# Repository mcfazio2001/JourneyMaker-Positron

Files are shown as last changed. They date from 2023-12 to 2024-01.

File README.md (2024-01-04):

<div align="center">

# JourneyMaker-Positron
voxolite

https://voxolite.com/

IMG_3391_(1)

## Our Discord
<br>

</div>

## About

JourneyMaker is a redesigned 3D printer that combines the best qualities of [Positron V3](https://github.com/KRALYN/PositronV3) and [Positron LT](https://github.com/Audiotronix/Positron_LT) with our own innovations. Perfect for hobbyists and professionals looking for a space-saving printing solution.

Built upon the innovative Positron V3 form factor and motion system by [KRALYN](https://github.com/KRALYN/PositronV3) and inspired by the Positron LT design, the JourneyMaker represents a combination of their standout features with our unique improvements. Many of the design improvements to the Positron printer come from the LT, while JourneyMaker integrates those into its own design. JourneyMaker simplifies all design complexities from the other Positron versions and enhances performance to make it the best Positron Printer available. 

Its compatibility with modifications tailored for other Positron versions makeing it an ideal choice for an enhanced printing experience while allowing flexibility for personalized adjustments.

</div>

## Advantages 

- Simplified assembly (The easiest Positron Printer to build)
- Cost reduction (Cost less than the Positron V3) 
- User-friendly build guide
- Integrated PSU (power supply unit) with 200W
- 3mm GT2 timing belt on XY (cheaper and easier to source than the original Synchromesh wire)
- Simplified Z axis by using a leadscrew. Easy to assemble by folding up
- Improved tool head cooling and heat creep
- Readily available machined parts (No need to machine your parts, we've got you covered. Vist Voxolite.com)
- Less machined parts than the Positron V3
- New extruder

</div>

## Specs

-	Max Print Speed: `250mm/s` (Not limited to)
-	Max Travel Speed: `350mm/s` (Not limited to)
-	Acceleration: `9800mm/s^2` (Not limited to)
-	Build Volume: `180x180x173mm`
-	Weight: `2600-3000g` (with integrated PSU)
-	Hotend max temp: `250C`
-	Build Plate Max temp: `80-100C`
-	Power supply: `24V; 200W`
-	Footprint: `~200mmx200mm`

</div>
<br>

## Build Instructions and Bill of Materials 
  
Link for the BOM:
https://docs.google.com/spreadsheets/d/1nYiwHz63ZsrtXtIAmWYqItgidqx7duSCUeQ9fUIy6CY/edit?usp=sharing

Link for the Instructions:
https://docs.google.com/presentation/d/1X3SdqvoahyYstLh0CLl6Gt2k5lkNw0UiuemN1DqQ030/edit?usp=sharing

</div>
<br>

## Help Support the Project 
If you like this design, please consider supporting the Voxolite team via donations; [Paypal](https://www.paypal.com/donate/?hosted_button_id=8HVCJBN4Q7MXC)

</div>
<br>

## License
<be>

General Overview:

- License Type: Creative Commons Attribution-NonCommercial 4.0 International.
- Licensing Entity: Creative Commons Corporation.
  
Important Definitions:

- Adapted Material: Material derived from or based upon the Licensed Material, requiring permission under the Copyright and Similar Rights.
- Licensed Material: The original work, database, or material covered by the license.

Scope of License:

- **License Grant: You are granted a worldwide, royalty-free, non-sublicensable, non-exclusive, irrevocable license for NonCommercial purposes only.**
- Exceptions and Limitations: The license does not apply if Exceptions and Limitations to Copyright and Similar Rights are in effect.
- Media and Formats: You are authorized to exercise the Licensed Rights in all media and formats, with technical modifications allowed.
- Downstream Recipients: Recipients automatically receive an offer to exercise the Licensed Rights.

License Conditions:

- **Attribution: If you share the material, you must provide attribution to the creator(s) and others designated, indicating modifications and license terms. This condition extends to Adapted Material.**

Sui Generis Database Rights:

- Specifics: Additional conditions apply if the Licensed Rights include Sui Generis Database Rights.

Disclaimer and Limitation of Liability:

- Warranties: The licensor provides the material as-is and makes no warranties.
- Limitation of Liability: The licensor is not liable for any losses, costs, or damages arising from the use of the material.

Term and Termination:

- Term: The license applies for the term of the Copyright and Similar Rights.
- Termination: Your rights terminate automatically if you fail to comply, but they can be reinstated under certain conditions.

Other Terms and Conditions:

- Additional Terms: The licensor is not bound by additional or different terms unless expressly agreed.

Interpretation:

- Non-Reduction: The license does not reduce, limit, or impose conditions on any lawful use without permission.
- Enforceability: Unenforceable provisions are automatically reformed or severed without affecting the rest.
- No Waiver: No waiver of terms or conditions unless expressly agreed.

Immunities:

- Privileges and Immunities: Nothing in the license limits the privileges and immunities that apply to the Licensor or You.

Important Note:

This summary is not a substitute for the actual license text, and it's crucial to read and understand the complete license terms for compliance. If you have specific questions or concerns, it's advisable to seek legal advice or consult the Creative Commons website.

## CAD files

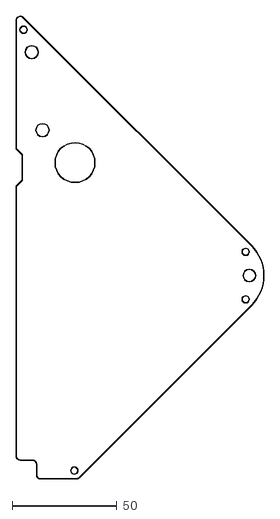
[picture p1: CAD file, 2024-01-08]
JourneyMaker STL Files/DXF Files (Optional)/TopPlate_Right.dxf
118.0 x 220.6

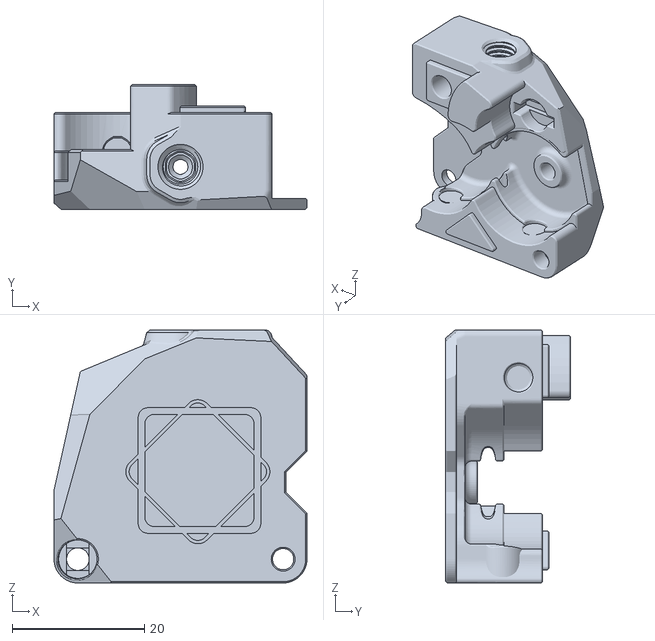
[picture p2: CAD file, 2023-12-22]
JourneyMaker STL Files/Extruder/Hummingbird_extruder_mod2 parts - Front_PC4_M6-1.stl
38.2 x 18.8 x 38.2

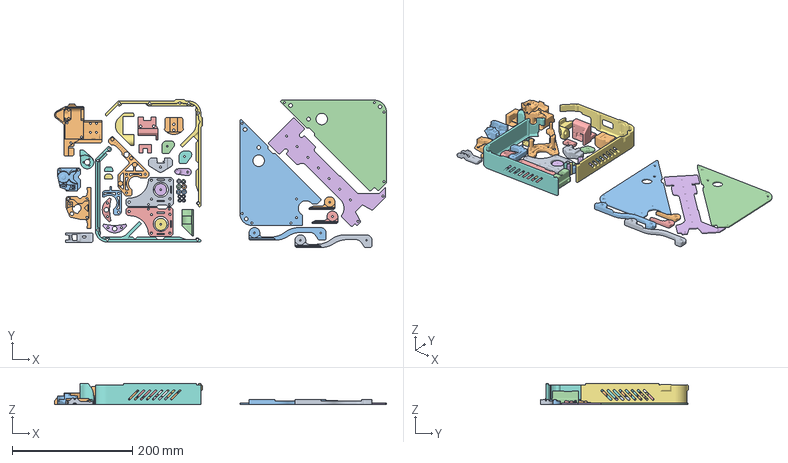
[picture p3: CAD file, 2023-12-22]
JourneyMaker STL Files/JourneyMaker.3mf
551.5 x 245.8 x 35.5 mm
Belt_Tensioner_XY V2.2 - Belt_Tensioner_XY.stl
Front_Pannel (1).stl
M3 x8.3_Spacers - M3 x11.5_Spacers.stl x 4
M3x5_Spacers (1).stl x 2
RasingClamp_For_BedHolder_Left (1).stl
RasingClamp_For_BedHolder_Left (2).stl
Side_Pannel_Left - Side_Pannel_Left.stl
Side_Pannel_Right - Side_Pannel_Right.stl
Spacer_3.2ID_6OD - Spacer_3.2ID_6OD.stl x 4
Tool Head (1).stl
TopPlate_Left_V2 - TopPlate_Left.stl
TopPlate_Right_V2 - TopPlate_Right.stl
Z Axis Bed Holder Connection (Mag Connector) - Z Axis Bed Holder Connection v3.stl
Z Axis Tensioner - Z Axis Tensioner.stl
Z Axis Top Mount (1).stl
Z Carriage Mount v2.2 - Z Carriage Mount.stl
x-axis_Motor_Bracket_v2 - x-axis_Motor_Bracket_Left.stl
z-Axis_Motor_Bracket Copy 1 - z-axis_Motor_Bracket.stl
z-Axis_Motor_Bracket Copy 1 - z-axis_Motor_TopPlate_Support.stl
z-axis-LeaderScrew_Bottom_Mount (2).stl
x-axis_Motor_Bracket_v2 - x-axis_Motor_Bracket_Right.stl
Belt connector (1).stl
Bed_Clamp - Bed_Clamp.stl x 2
SpoolHolder Part 3.stl x 2
SpoolHolder Part 2.stl x 2
SpoolHolder Part 1.stl x 2
Center_Pannel - PCB Cover.stl
x-Rail_Endcap (1).stl x 2
Hummingbird_extruder_mod2 parts - Arm^Hummingbird_extruder_5.stl
Hummingbird_extruder_mod2 parts - Back.stl
Hummingbird_extruder_mod2 parts - Front_PC4_M6-1.stl

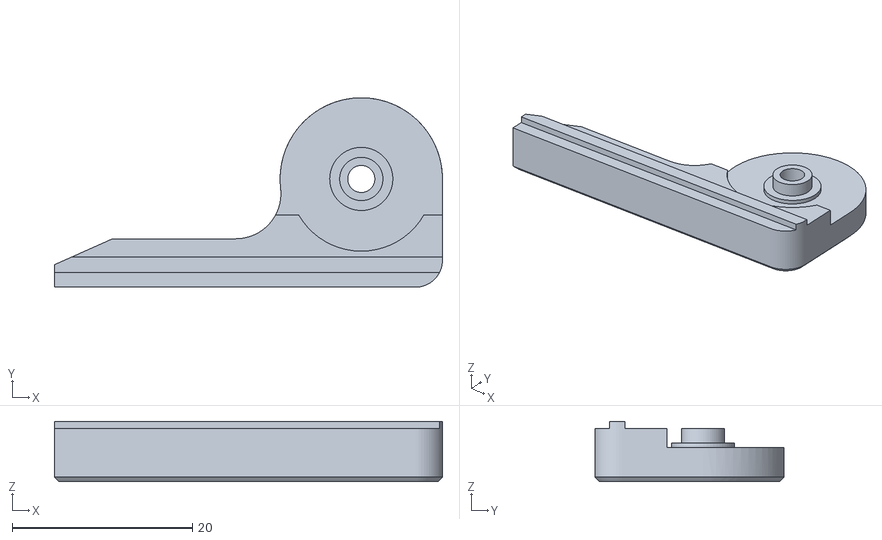
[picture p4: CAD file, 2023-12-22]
JourneyMaker STL Files/Spool_Holder/SpoolHolder Part 1.stl
43.0 x 21.0 x 6.70

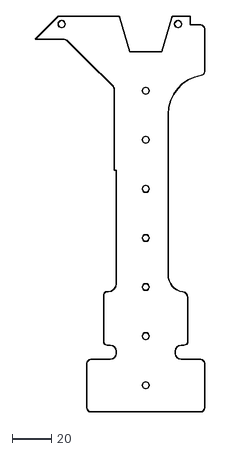
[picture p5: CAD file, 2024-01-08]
JourneyMaker STL Files/DXF Files (Optional)/Center_Pannel.dxf
86.2 x 201.6

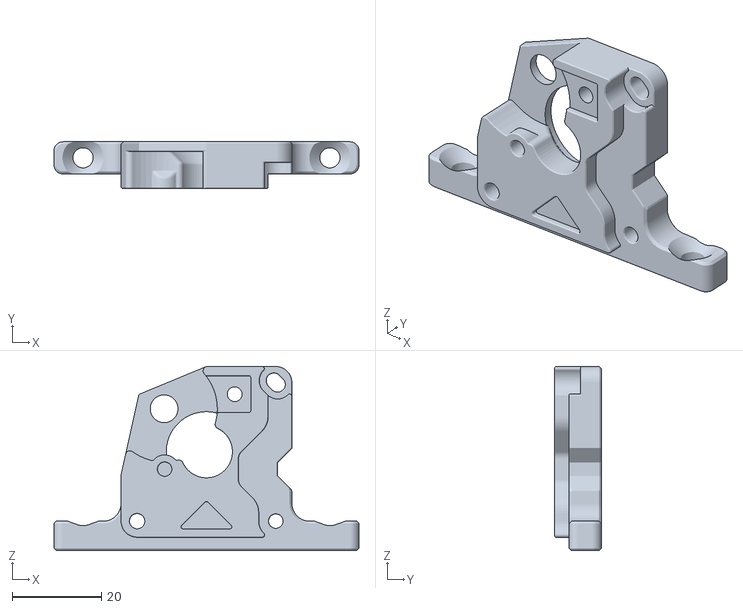
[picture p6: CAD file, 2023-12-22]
JourneyMaker STL Files/Extruder/Hummingbird_extruder_mod2 parts - Back.stl
68.2 x 10.4 x 41.2

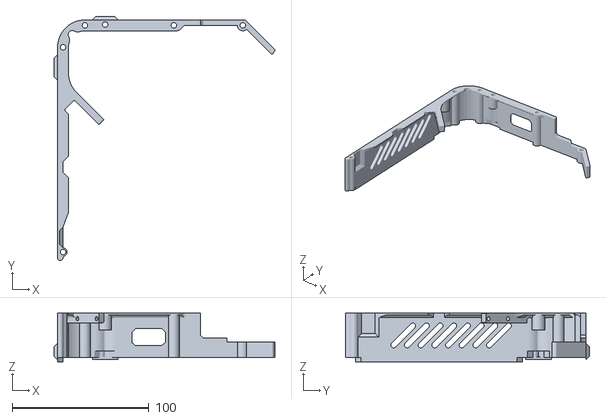
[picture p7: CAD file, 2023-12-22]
JourneyMaker STL Files/Main Parts/Side_Pannel_Left - Side_Pannel_Left.stl
161.3 x 178.3 x 35.5

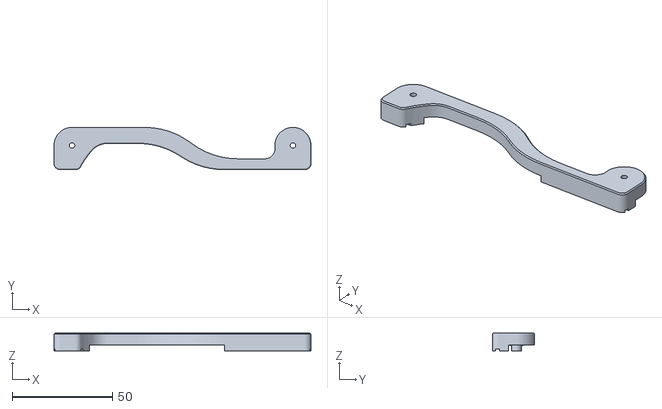
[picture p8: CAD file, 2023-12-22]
JourneyMaker STL Files/Spool_Holder/SpoolHolder Part 2.stl
128.0 x 21.0 x 8.90

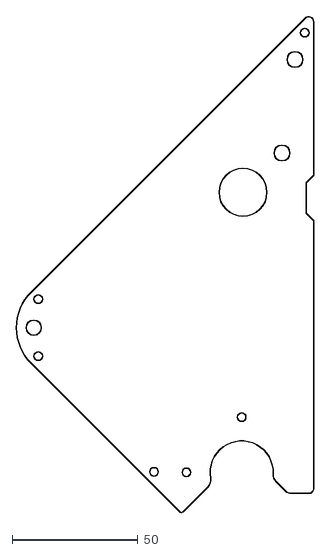
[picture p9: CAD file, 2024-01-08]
JourneyMaker STL Files/DXF Files (Optional)/TopPlate_Left.dxf
118.0 x 197.2

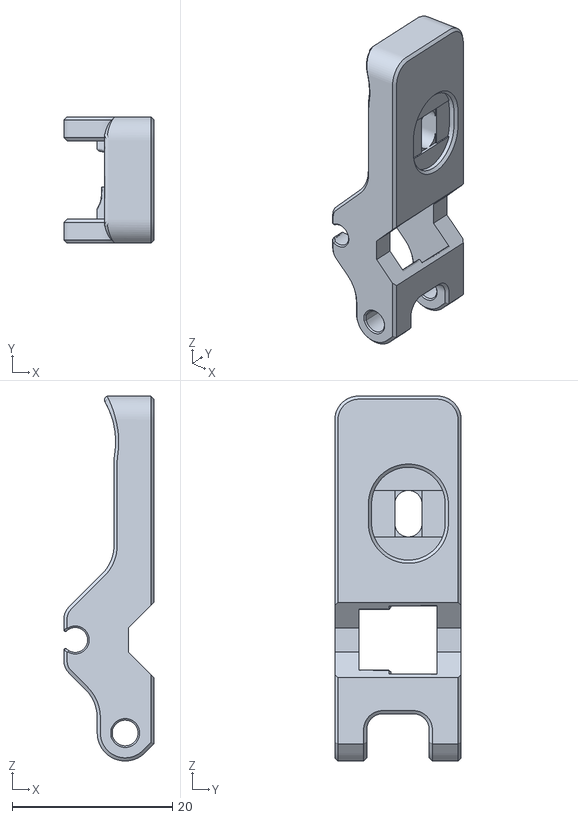
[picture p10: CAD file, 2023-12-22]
JourneyMaker STL Files/Extruder/Hummingbird_extruder_mod2 parts - Arm^Hummingbird_extruder_5.stl
11.2 x 15.8 x 45.6

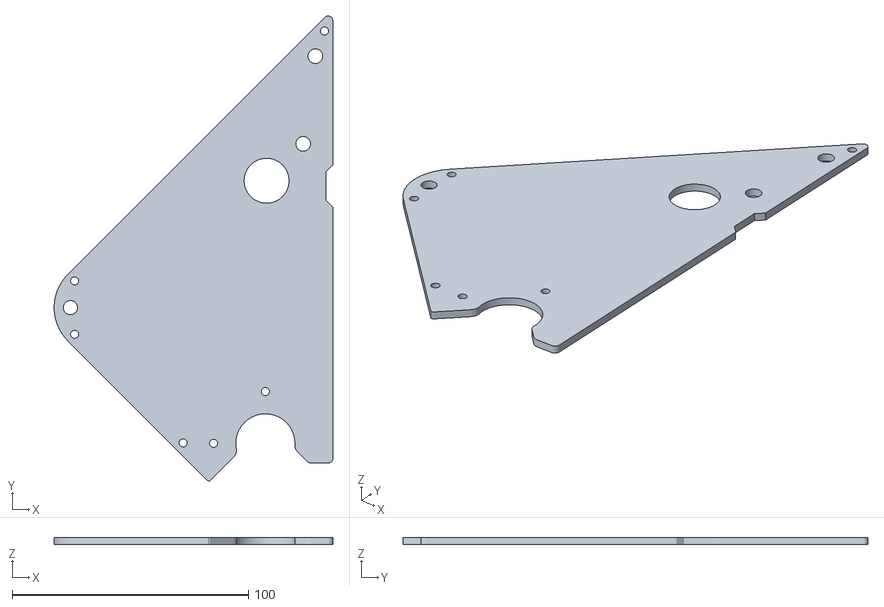
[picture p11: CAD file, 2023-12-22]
JourneyMaker STL Files/Main Parts/TopPlate_Left_V2 - TopPlate_Left.stl
118.0 x 196.9 x 3.00

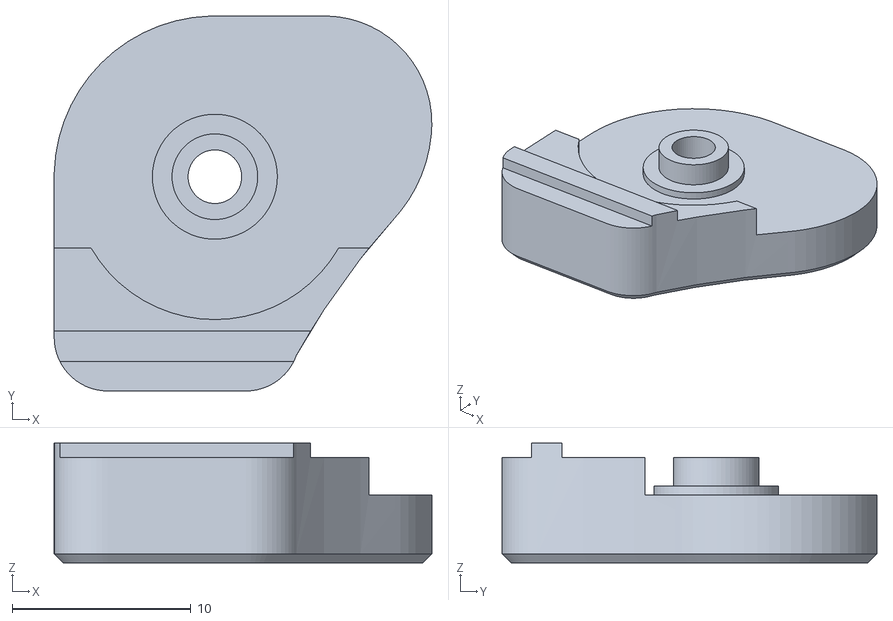
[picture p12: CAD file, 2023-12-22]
JourneyMaker STL Files/Spool_Holder/SpoolHolder Part 3.stl
21.1 x 21.0 x 6.70

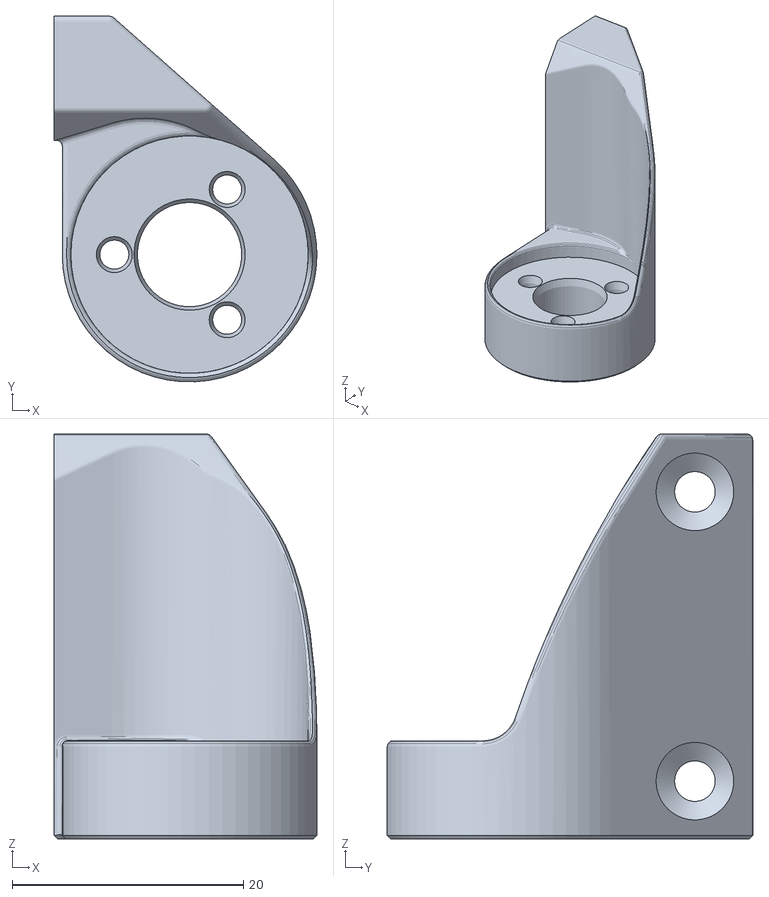
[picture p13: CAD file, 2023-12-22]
JourneyMaker STL Files/Main Parts/Z Carriage Mount v2.2 - Z Carriage Mount.stl
22.7 x 31.6 x 35.0

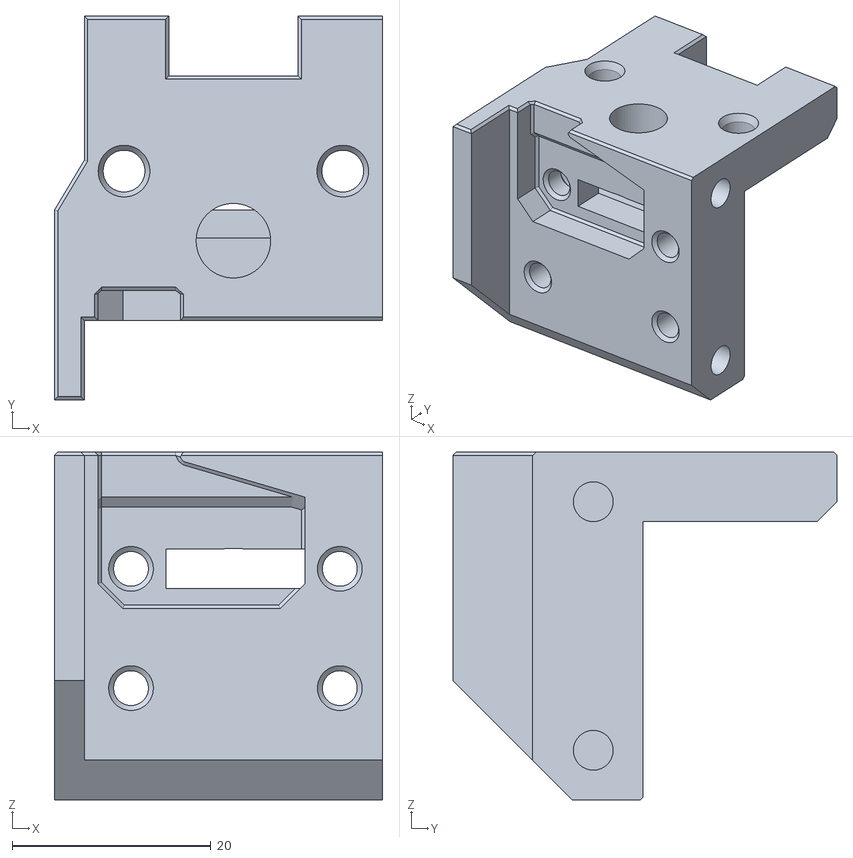
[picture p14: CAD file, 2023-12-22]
JourneyMaker STL Files/Main Parts/Z Axis Bed Holder Connection (Mag Connector) - Z Axis Bed Holder Connection v3.stl
33.0 x 38.6 x 35.0

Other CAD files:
JourneyMaker STL Files/Main Parts/TopPlate_Right_V2 - TopPlate_Right.stl
JourneyMaker STL Files/Main Parts/Spacer_3.2ID_6OD - Spacer_3.2ID_6OD.stl
JourneyMaker STL Files/Main Parts/RasingClamp_For_BedHolder_Left (1).stl
JourneyMaker STL Files/Main Parts/x-axis_Motor_Bracket_v2 - x-axis_Motor_Bracket_Right.stl
JourneyMaker STL Files/Main Parts/Bed_Clamp - Bed_Clamp.stl
JourneyMaker STL Files/Main Parts/Belt connector (1).stl
JourneyMaker STL Files/Main Parts/Belt_Tensioner_XY V2.2 - Belt_Tensioner_XY.stl
JourneyMaker STL Files/Main Parts/Center_Pannel - PCB Cover.stl
JourneyMaker STL Files/Main Parts/Front_Pannel (1).stl
JourneyMaker STL Files/Main Parts/M3 x8.3_Spacers - M3 x11.5_Spacers.stl
JourneyMaker STL Files/Main Parts/M3x5_Spacers (1).stl
JourneyMaker STL Files/Main Parts/RasingClamp_For_BedHolder_Left (2).stl
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

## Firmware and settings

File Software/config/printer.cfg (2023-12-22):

[include mainsail.cfg]

[printer]
kinematics: corexy
max_velocity: 500
max_accel: 15000
max_accel_to_decel: 10000
square_corner_velocity: 5 
max_z_velocity: 50
max_z_accel: 200

[mcu]
serial: /dev/serial0
baud: 250000
restart_method: command

[stepper_y]
step_pin: gpio11
dir_pin: gpio10
enable_pin: !gpio12
microsteps: 16
rotation_distance: 40
endstop_pin: tmc2209_stepper_y:virtual_endstop
homing_retract_dist: 0
position_endstop: 0
position_max: 170
homing_speed: 20
#homing_positive_dir: True

[tmc2209 stepper_y]
uart_pin: gpio9
tx_pin: gpio8
uart_address: 0
run_current: 0.7
stealthchop_threshold: 999999
diag_pin: ^gpio4
driver_SGTHRS: 45

[stepper_x]
step_pin: gpio6
dir_pin: gpio5
enable_pin: !gpio7
microsteps: 16
rotation_distance: 40
endstop_pin: tmc2209_stepper_x:virtual_endstop
homing_retract_dist: 0
position_endstop: 0
position_max: 185
homing_speed: 20

[tmc2209 stepper_x]
uart_pin: gpio9
tx_pin: gpio8
uart_address: 2
run_current: 0.7
stealthchop_threshold: 999999
diag_pin: ^gpio3
driver_SGTHRS: 35

[stepper_z]
step_pin: gpio19
dir_pin: gpio28
enable_pin: !gpio2
microsteps: 16
rotation_distance: 4
endstop_pin: probe:z_virtual_endstop
position_min: -2.5
position_max: 173
homing_speed: 5

[tmc2209 stepper_z]
uart_pin: gpio9
tx_pin: gpio8
uart_address: 1
run_current: 0.4
stealthchop_threshold: 999999

[extruder]
step_pin: gpio14
dir_pin: !gpio13 #change this for direction
enable_pin: !gpio15
microsteps: 16

###V2 Extruder
full_steps_per_rotation: 200
rotation_distance: 53.494165  
gear_ratio: 44:10, 37:17

#rotation_distance: 4.92 #v1 Extruder

nozzle_diameter: 0.4
filament_diameter: 1.75
heater_pin: gpio23 
sensor_type: Generic 3950
sensor_pin: gpio27
control: pid
pid_Kp: 25.12
pid_Ki: 1.073
pid_Kd: 147
min_temp: -100
max_temp: 260
max_extrude_cross_section:2
pressure_advance: 0.43 #0.32
min_extrude_temp: 170 #0 for testing 
max_extrude_only_distance: 400

[tmc2209 extruder]
uart_pin: gpio9
tx_pin: gpio8
uart_address: 3
run_current: 0.69
hold_current: 0.4
stealthchop_threshold: 999999

[heater_bed]
heater_pin: gpio21
sensor_type: ATC Semitec 104NT-4-R025H42G
sensor_pin: gpio26
pwm_cycle_time: 0.015
max_power: 1.0
control: pid
pid_Kp: 56.852
pid_Ki: 2.1
pid_Kd: 383.75
min_temp: -100
max_temp: 85

[controller_fan mcu_fan]
pin: gpio17
max_power: 0.8
shutdown_speed: 0
cycle_time: 0.01
kick_start_time: 1
fan_speed: 0.8
idle_timeout: 5
stepper: stepper_x, stepper_y, stepper_z


[heater_fan nozzle_cooling_fan]
pin: gpio20
max_power: 0.7
kick_start_time: 1
shutdown_speed: 0

[fan]
pin: gpio18
kick_start_time: 1
max_power: 0.9
shutdown_speed: 0

[force_move]
enable_force_move = true

[gcode_macro FORCE_Z_UP]
gcode: FORCE_MOVE STEPPER=stepper_z DISTANCE=30 VELOCITY=40

[virtual_sdcard]
path: /home/3dprinter/printer_data/gcodes

[probe]
pin: ^gpio25
x_offset:55
y_offset: 30
#z_offset: 0.8
speed: 3
samples: 3
sample_retract_dist: 0.7

[bed_tilt]
points: 
  4, 14
  130, 14
  130, 100
  35, 100
speed: 150
horizontal_move_z: 4

[gcode_arcs]
resolution: 1.0

[homing_override]
gcode: # Please manually set Homing speed to about half of rotation_distance (28 for synchromesh positron)
  {% set HOME_CUR = 1.000 %} # higher current on steppers makes sensorless homing more reliable
  {% set HOME_SENS_X_AXIS = 35 %} #Set this value for stepper sensitivity during X-Axis Homing
  {% set HOME_SENS_Y_AXIS = 35 %} #Set this value for stepper sensitivity during Y-Axis Homing
  # Retrieve used setting for stepper current and save them
  {% set RUN_CUR_X_STEPPER = printer.configfile.settings['tmc2209 stepper_x'].run_current %}
  {% set RUN_CUR_Y_STEPPER = printer.configfile.settings['tmc2209 stepper_y'].run_current %}
  # Retrieve used setting for stepper sensitivity and save them
  {% set RUN_SENS_X_STEPPER = printer.configfile.settings['tmc2209 stepper_x'].driver_sgthrs %}
  {% set RUN_SENS_Y_STEPPER = printer.configfile.settings['tmc2209 stepper_y'].driver_sgthrs %}
  # Set current for sensorless homing
  SET_TMC_CURRENT STEPPER=stepper_x CURRENT={HOME_CUR}
  SET_TMC_CURRENT STEPPER=stepper_y CURRENT={HOME_CUR}
  # Pause to ensure driver stall flag is clear
  G4 P500
  #Make printer believe we are at 0 0 0 so we can move Y axis back towards center later
  SET_KINEMATIC_POSITION X=0
  SET_KINEMATIC_POSITION Y=0
  SET_KINEMATIC_POSITION Z=0
  # Home X
  SET_TMC_FIELD STEPPER=stepper_x FIELD=SGTHRS VALUE={HOME_SENS_X_AXIS}
  SET_TMC_FIELD STEPPER=stepper_y FIELD=SGTHRS VALUE={HOME_SENS_X_AXIS}
  G28 X0
  G0 X10 F5000
  G4 P500
  # Home Y
  SET_TMC_FIELD STEPPER=stepper_x FIELD=SGTHRS VALUE={HOME_SENS_Y_AXIS}
  SET_TMC_FIELD STEPPER=stepper_y FIELD=SGTHRS VALUE={HOME_SENS_Y_AXIS}
  G28 Y0
  G0 Y10 F5000
  G4 P500
  # Home Z
  G0 X100 Y100 F5000
  G28 Z0
  # Set current back to regular values because we don't need to print with the higher currents on motors
  SET_TMC_CURRENT STEPPER=stepper_x CURRENT={RUN_CUR_X_STEPPER}
  SET_TMC_CURRENT STEPPER=stepper_y CURRENT={RUN_CUR_Y_STEPPER}
  # Set sensitivity back to regular values
  SET_TMC_FIELD STEPPER=stepper_x FIELD=SGTHRS VALUE={RUN_SENS_X_STEPPER}
  SET_TMC_FIELD STEPPER=stepper_y FIELD=SGTHRS VALUE={RUN_SENS_Y_STEPPER}


[gcode_macro UNLOAD_FILAMENT]
gcode:
  M83 
  G1 E-30 F1800
  G1 E-100 F1200
  G1 E-100 F1200
  G1 E-100 F1200
  G1 E-100 F1200
  G1 E-100 F1200
  G92 E0
  G90

[gcode_macro LOAD_FILAMENT]
gcode:
  M83 
  G1 E100 F1200
  G1 E100 F1200
  G1 E100 F1200
  G1 E100 F1200
  G1 E50 F1200
  G1 E40 F800
  G92 E0
  G90

[gcode_macro PRINT_START]
gcode:
  {% set BED_TEMP = params.BED|default(60)|float %}
  {% set PLATE_TEMP = params.BED|default(50)|float * 0.87 %}
  {% set EXTRUDER_TEMP = params.EXTRUDER|default(190)|float %}

  SET_LED LED=WS2812 RED=0 GREEN=0.1 BLUE=0.2   ; color teal
  M140 S{BED_TEMP}                              ; set bed temperature and continue
  M104 S{EXTRUDER_TEMP}                         ; set hotend temperature and continue
  M106 S190                                     ; fan on for correct PID
  G4  P3000                                     ; wait 3 sec
  G28                                           ; Home all axes
  G1 Z40 F300                                   ; Z raise
  G1 X5 Y80 F3000                               ; go to parking pos.
  M109 S{EXTRUDER_TEMP}                         ; wait for hot end temperature to reach e.g. 210C
  M106 S0                                       ; fan off
  SET_LED LED=WS2812 RED=0.18 GREEN=0 BLUE=0.20 ; color purple
  #G29                                           ; Level bed; Activate bed leveling compensation
  #BED_TILT_CALIBRATE
  SET_LED LED=WS2812 RED=0.2 GREEN=0.1 BLUE=0   ; color orange - printing color
  G4  P1000                                     ; wait a second

  # prime nozzle
  G1 X30 Y5 F7200                               ; move to start
  G1 Z0.3 F800                                  ; Move to layer height
  G1 X130 Y5 E20 F800                           ; print prime line
  G1 X130 Y5 F7200                              ; move to start
  G1 X30 Y5 E40 F800                            ; print prime line
  #SET_SKEW XY=142.72,140.8,100.3

[gcode_macro PRINT_END]
gcode:
  SET_LED LED=WS2812 RED=0.1 GREEN=0.35 BLUE=0 ; finished printing: green
  M104 S0
  M140 S0
  
  # Retract the filament
  G92 E1
  G1 E-1 F80
  SET_SKEW CLEAR=1
  G1 X5 Y90 F3000
  G91
  G1 Z20 F600
  G1 Z20 F600
  G1 Z20 F600
  G1 Z20 F600
  G90
  M84
  G4  P1000 ; wait a second
  SET_LED LED=WS2812 RED=0.1 GREEN=0.1 BLUE=0.1 ; default: white
  G1 Z80 F300

[gcode_macro G29]
gcode:
  G28
  G1 Z5 F800
	BED_TILT_CALIBRATE

[delayed_gcode my_delayed_gcode]
gcode:
    SET_LED LED=WS2812 RED=0 GREEN=0.05 BLUE=0.01 INDEX=3
    SET_LED LED=WS2812 RED=0.1 GREEN=0.1 BLUE=0.05 INDEX=2
    SET_LED LED=WS2812 RED=0.1 GREEN=0.1 BLUE=0.05 INDEX=1
    G4 P100
    SET_LED LED=WS2812 RED=0 GREEN=0.1 BLUE=0.02 INDEX=3
    SET_LED LED=WS2812 RED=0.2 GREEN=0.2 BLUE=0.1 INDEX=2
    SET_LED LED=WS2812 RED=0.2 GREEN=0.2 BLUE=0.1 INDEX=1
    G4 P100
    SET_LED LED=WS2812 RED=0 GREEN=0.15 BLUE=0.04 INDEX=3
    SET_LED LED=WS2812 RED=0.3 GREEN=0.3 BLUE=0.15 INDEX=2
    SET_LED LED=WS2812 RED=0.3 GREEN=0.3 BLUE=0.15 INDEX=1
    G4 P100
    SET_LED LED=WS2812 RED=0 GREEN=0.2 BLUE=0.05 INDEX=3
    SET_LED LED=WS2812 RED=0.4 GREEN=0.4 BLUE=0.2 INDEX=2
    SET_LED LED=WS2812 RED=0.4 GREEN=0.4 BLUE=0.2 INDEX=1
    G4 P100
    SET_LED LED=WS2812 RED=0 GREEN=0.3 BLUE=0.1 INDEX=3
    SET_LED LED=WS2812 RED=0.5 GREEN=0.5 BLUE=0.25 INDEX=2
    SET_LED LED=WS2812 RED=0.5 GREEN=0.5 BLUE=0.25 INDEX=1
    G4 P100
    SET_LED LED=WS2812 RED=0.6 GREEN=0.6 BLUE=0.3 INDEX=2
    SET_LED LED=WS2812 RED=0.6 GREEN=0.6 BLUE=0.3 INDEX=1
    G4 P100
    SET_LED LED=WS2812 RED=0.7 GREEN=0.7 BLUE=0.35 INDEX=2
    SET_LED LED=WS2812 RED=0.7 GREEN=0.7 BLUE=0.35 INDEX=1
    G4 P100
    SET_LED LED=WS2812 RED=0.9 GREEN=0.9 BLUE=0.45 INDEX=2
    SET_LED LED=WS2812 RED=0.9 GREEN=0.9 BLUE=0.45 INDEX=1
initial_duration: 0.1

[pause_resume]
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
